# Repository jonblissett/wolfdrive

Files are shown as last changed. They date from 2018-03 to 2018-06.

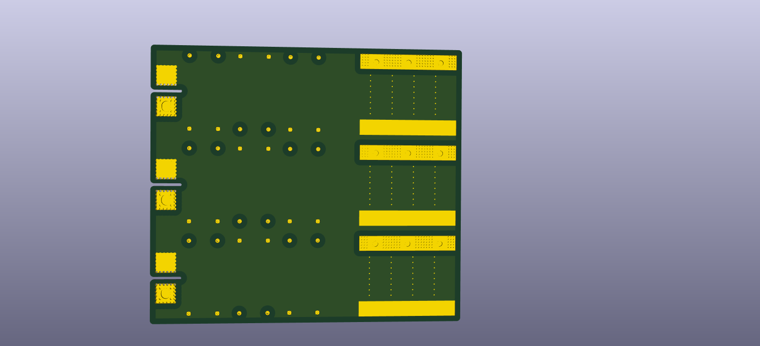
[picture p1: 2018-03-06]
DCbus/WolfDrive_DCbus_fab/WolfDrive_DCbus_back.png

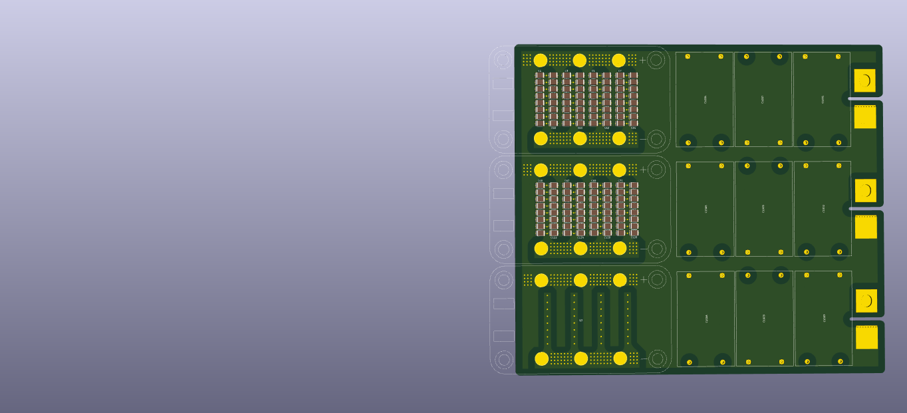
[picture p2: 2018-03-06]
DCbus/WolfDrive_DCbus.png

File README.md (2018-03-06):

# wolfdrive
Motor drive inverter designed to be used with the Cree CAS325M12HM2 silicon carbide MOSFETs.

Anticipated specifications:
Peak power, 250kW
Current, ~300Arms
DC bus voltage, <800Vdc

## /controller

Control board, using STM32H743 microcontroller. Accepts analogue signals for throttle, will output FOC signals to gate drivers.

## /firmware

Software repository for controller - currently empty!

## /DCbus

PCB to connect DC bus capacitors with low stray inductance

## /DCsnubber

Alternative DC bus capacitor connection for small capacitors above devices like in early evaluation kit from Cree. May work out to be a cheaper option than /DCbus.

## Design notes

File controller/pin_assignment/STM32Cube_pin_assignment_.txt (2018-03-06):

Configuration	STM32Cube_pin_assignment_
STM32CubeMX 	4.23.0
Date	11/22/2017
MCU	STM32H743ZITx

PERIPHERALS	MODES	FUNCTIONS	PINS
ADC2	IN5 Single-ended	ADC2_INP5	PB1
ETH	RMII	ETH_CRS_DV	PA7
ETH	RMII	ETH_MDC	PC1
ETH	RMII	ETH_MDIO	PA2
ETH	RMII	ETH_REF_CLK	PA1
ETH	RMII	ETH_RXD0	PC4
ETH	RMII	ETH_RXD1	PC5
ETH	RMII	ETH_TXD0	PB12
ETH	RMII	ETH_TXD1	PB13
ETH	RMII	ETH_TX_EN	PB11
QUADSPI	Bank1 with Quad SPI Lines	QUADSPI_BK1_IO0	PD11
QUADSPI	Bank1 with Quad SPI Lines	QUADSPI_BK1_IO1	PD12
QUADSPI	Bank1 with Quad SPI Lines	QUADSPI_BK1_IO2	PE2
QUADSPI	Bank1 with Quad SPI Lines	QUADSPI_BK1_IO3	PD13
QUADSPI	Bank1 with Quad SPI Lines	QUADSPI_BK1_NCS	PB10
QUADSPI	Bank1 with Quad SPI Lines	QUADSPI_CLK	PB2
SDMMC1	SD 4 bits Wide bus	SDMMC1_CK	PC12
SDMMC1	SD 4 bits Wide bus	SDMMC1_CMD	PD2
SDMMC1	SD 4 bits Wide bus	SDMMC1_D0	PC8
SDMMC1	SD 4 bits Wide bus	SDMMC1_D1	PC9
SDMMC1	SD 4 bits Wide bus	SDMMC1_D2	PC10
SDMMC1	SD 4 bits Wide bus	SDMMC1_D3	PC11
SPI1	Full-Duplex Master	SPI1_MISO	PA6
SPI1	Full-Duplex Master	SPI1_MOSI	PD7
SPI1	Full-Duplex Master	SPI1_SCK	PA5
SPI1	Hardware NSS Output Signal	SPI1_NSS	PA15
SPI2	Full-Duplex Master	SPI2_MISO	PC2_C
SPI2	Full-Duplex Master	SPI2_MOSI	PB15
SPI2	Full-Duplex Master	SPI2_SCK	PD3
SPI2	Hardware NSS Output Signal	SPI2_NSS	PB4
SYS	Serial Wire	SYS_JTCK-SWCLK	PA14
SYS	Serial Wire	SYS_JTMS-SWDIO	PA13
SYS	SysTick	SYS_VS_Systick	VP_SYS_VS_Systick
TIM1	Internal Clock	TIM1_VS_ClockSourceINT	VP_TIM1_VS_ClockSourceINT
TIM1	PWM Generation CH1 CH1N	TIM1_CH1	PE9
TIM1	PWM Generation CH1 CH1N	TIM1_CH1N	PE8
TIM1	PWM Generation CH2 CH2N	TIM1_CH2	PE11
TIM1	PWM Generation CH2 CH2N	TIM1_CH2N	PE10
TIM1	Output Compare CH3 CH3N	TIM1_CH3	PE13
TIM1	Output Compare CH3 CH3N	TIM1_CH3N	PE12
USART6	Asynchronous	USART6_RX	PG9
USART6	Asynchronous	USART6_TX	PG14

Pin Nb	PINs	FUNCTIONs	LABELs
1	PE2	QUADSPI_BK1_IO2	
27	PC1	ETH_MDC	
28	PC2_C	SPI2_MISO	
35	PA1	ETH_REF_CLK	
36	PA2	ETH_MDIO	
41	PA5	SPI1_SCK	
42	PA6	SPI1_MISO	
43	PA7	ETH_CRS_DV	
44	PC4	ETH_RXD0	
45	PC5	ETH_RXD1	
47	PB1	ADC2_INP5	
48	PB2	QUADSPI_CLK	
59	PE8	TIM1_CH1N	
60	PE9	TIM1_CH1	
63	PE10	TIM1_CH2N	
64	PE11	TIM1_CH2	
65	PE12	TIM1_CH3N	
66	PE13	TIM1_CH3	
69	PB10	QUADSPI_BK1_NCS	
70	PB11	ETH_TX_EN	
73	PB12	ETH_TXD0	
74	PB13	ETH_TXD1	
76	PB15	SPI2_MOSI	
80	PD11	QUADSPI_BK1_IO0	
81	PD12	QUADSPI_BK1_IO1	
82	PD13	QUADSPI_BK1_IO3	
98	PC8	SDMMC1_D0	
99	PC9	SDMMC1_D1	
105	PA13	SYS_JTMS-SWDIO	
109	PA14	SYS_JTCK-SWCLK	
110	PA15	SPI1_NSS	
111	PC10	SDMMC1_D2	
112	PC11	SDMMC1_D3	
113	PC12	SDMMC1_CK	
116	PD2	SDMMC1_CMD	
117	PD3	SPI2_SCK	
123	PD7	SPI1_MOSI	
124	PG9	USART6_RX	
129	PG14	USART6_TX	
134	PB4	SPI2_NSS

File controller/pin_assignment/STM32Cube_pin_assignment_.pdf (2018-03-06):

## STM32Cube_pin_assignment_ Project Configuration Report

# 1. Description

## 1.1. Project

Project Name | STM32Cube_pin_assignment_
Board Name | No information
Generated with: | STM32CubeMX 4.23.0
Date | 11/22/2017

## 1.2. MCU

MCU Series | STM32H7
MCU Line | STM32H7x3
MCU name | STM32H743ZITx
MCU Package | LQFP144
MCU Pin number | 144

# 2. Pinout Configuration

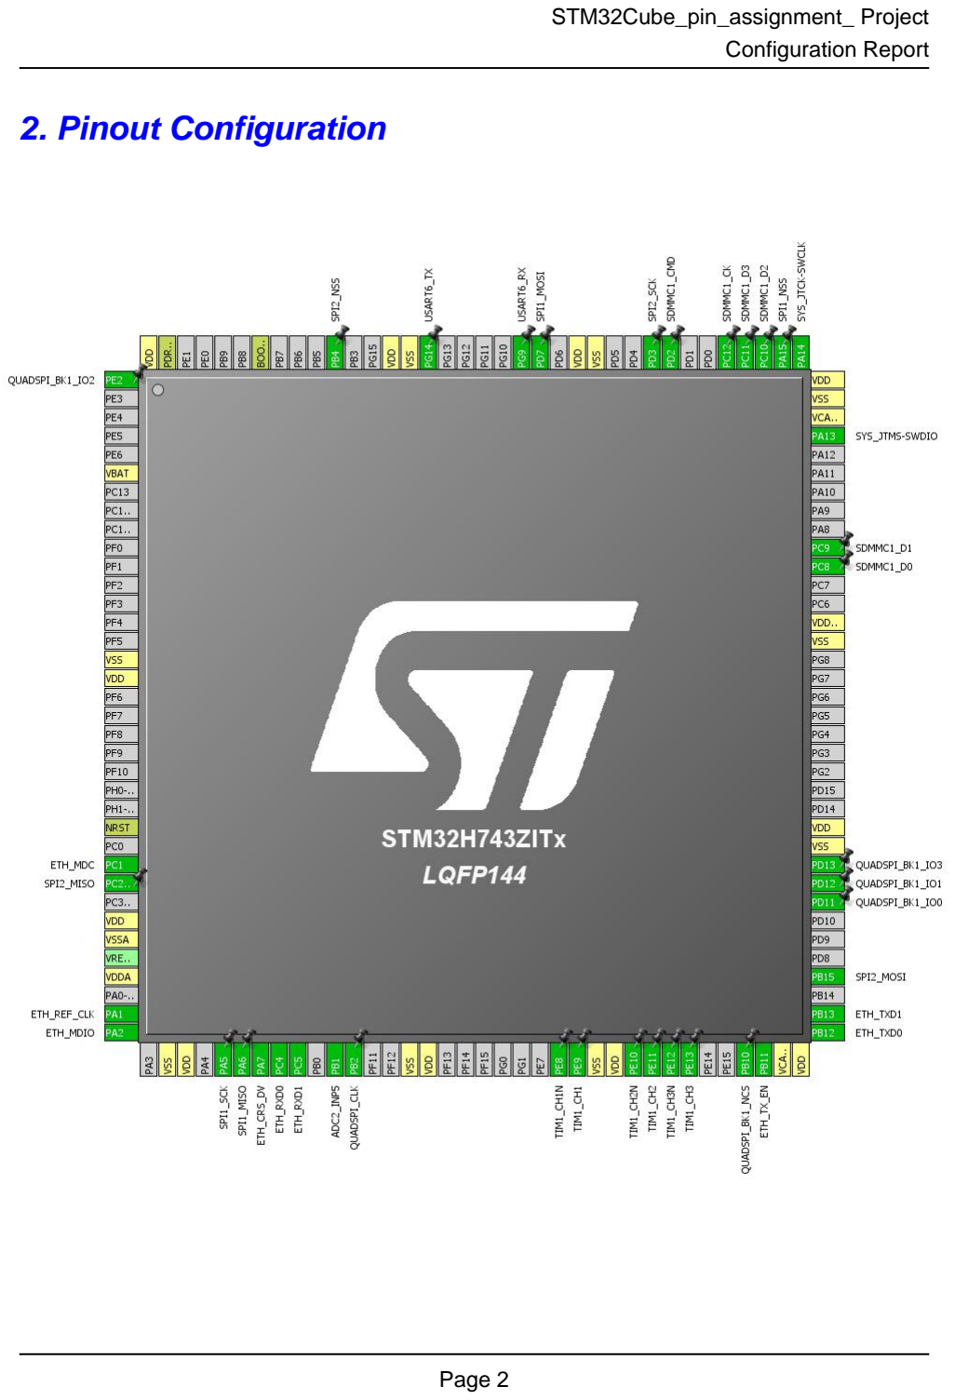
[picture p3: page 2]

# 3. Pins Configuration

Pin Number LQFP144 | Pin Name (function after reset) | Pin Type | Alternate Function(s) | Label
1 | PE2 | I/O | QUADSPI_BK1_IO2
6 | VBAT | Power
16 | VSS | Power
17 | VDD | Power
25 | NRST | Reset
27 | PC1 | I/O | ETH_MDC
28 | PC2_C | I/O | SPI2_MISO
30 | VDD | Power
31 | VSSA | Power
33 | VDDA | Power
35 | PA1 | I/O | ETH_REF_CLK
36 | PA2 | I/O | ETH_MDIO
38 | VSS | Power
39 | VDD | Power
41 | PA5 | I/O | SPI1_SCK
42 | PA6 | I/O | SPI1_MISO
43 | PA7 | I/O | ETH_CRS_DV
44 | PC4 | I/O | ETH_RXD0
45 | PC5 | I/O | ETH_RXD1
47 | PB1 | I/O | ADC2_INP5
48 | PB2 | I/O | QUADSPI_CLK
51 | VSS | Power
52 | VDD | Power
59 | PE8 | I/O | TIM1_CH1N
60 | PE9 | I/O | TIM1_CH1
61 | VSS | Power
62 | VDD | Power
63 | PE10 | I/O | TIM1_CH2N
64 | PE11 | I/O | TIM1_CH2
65 | PE12 | I/O | TIM1_CH3N
66 | PE13 | I/O | TIM1_CH3
69 | PB10 | I/O | QUADSPI_BK1_NCS
70 | PB11 | I/O | ETH_TX_EN
71 | VCAP1 | Power
72 | VDD | Power
73 | PB12 | I/O | ETH_TXD0

Pin Number LQFP144 | Pin Name (function after reset) | Pin Type | Alternate Function(s) | Label
74 | PB13 | I/O | ETH_TXD1
76 | PB15 | I/O | SPI2_MOSI
80 | PD11 | I/O | QUADSPI_BK1_IO0
81 | PD12 | I/O | QUADSPI_BK1_IO1
82 | PD13 | I/O | QUADSPI_BK1_IO3
83 | VSS | Power
84 | VDD | Power
94 | VSS | Power
95 | VDD33_USB | Power
98 | PC8 | I/O | SDMMC1_D0
99 | PC9 | I/O | SDMMC1_D1
105 | PA13 | I/O | SYS_JTMS-SWDIO
106 | VCAP2 | Power
107 | VSS | Power
108 | VDD | Power
109 | PA14 | I/O | SYS_JTCK-SWCLK
110 | PA15 | I/O | SPI1_NSS
111 | PC10 | I/O | SDMMC1_D2
112 | PC11 | I/O | SDMMC1_D3
113 | PC12 | I/O | SDMMC1_CK
116 | PD2 | I/O | SDMMC1_CMD
117 | PD3 | I/O | SPI2_SCK
120 | VSS | Power
121 | VDD | Power
123 | PD7 | I/O | SPI1_MOSI
124 | PG9 | I/O | USART6_RX
129 | PG14 | I/O | USART6_TX
130 | VSS | Power
131 | VDD | Power
134 | PB4 | I/O | SPI2_NSS
138 | BOOT0 | Boot
143 | PDR_ON | Reset
144 | VDD | Power

# 4. Clock Tree Configuration

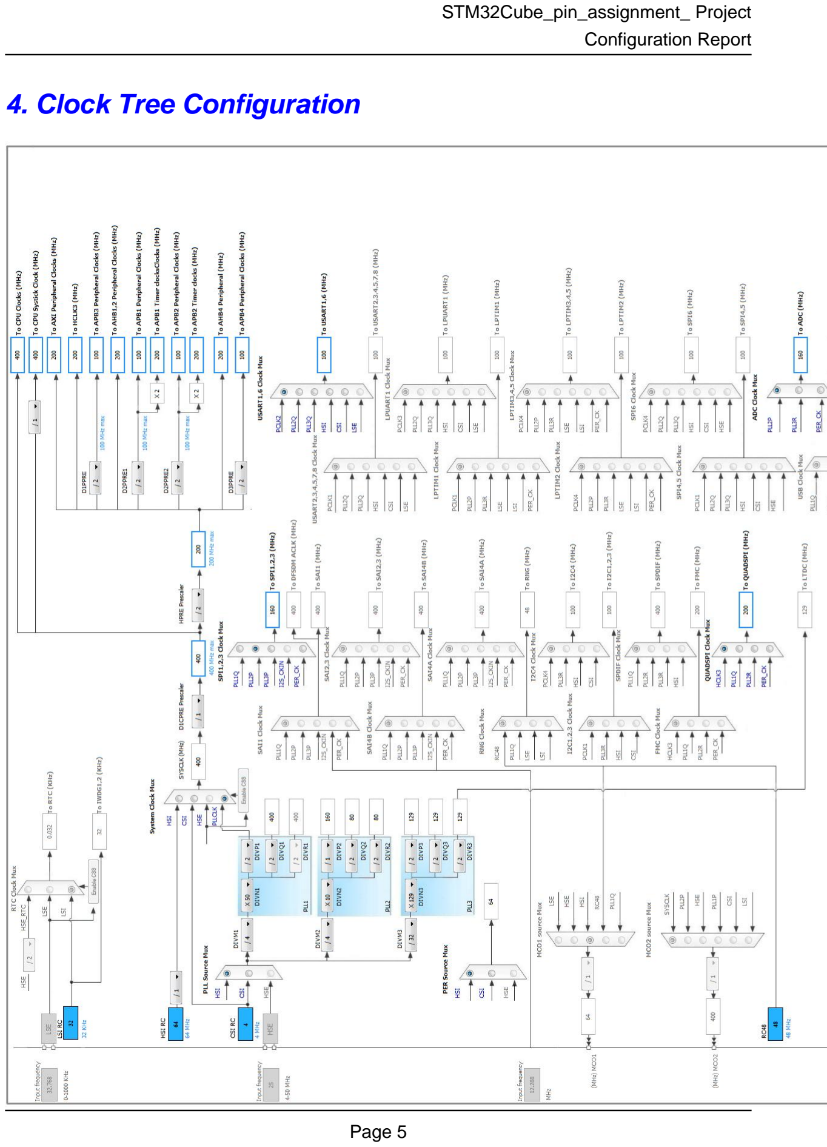
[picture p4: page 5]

# 5. IPs and Middleware Configuration

# 5.1. ADC2

## IN5: IN5 Single-ended

## 5.1.1. Parameter Settings:

### ADCs_Common_Settings:

Mode | Independent mode

### ADC_Settings:

Clock Prescaler | Asynchronous clock mode divided by 6
Resolution | ADC 16-bit resolution
Scan Conversion Mode | Disabled
Continuous Conversion Mode | Disabled
Discontinuous Conversion Mode | Disabled
DMA Continuous Requests | Disabled
End Of Conversion Selection | End of single conversion
Overrun behaviour | Overrun data preserved
Boost Mode | Enabled
Conversion Data Management Mode | Regular Conversion data stored in DR register only
Low Power Auto Wait | Disabled

### ADC_Regular_ConversionMode:

Enable Regular Conversions | Enable
Left Bit Shift | No bit shift
Enable Regular Oversampling | Disable
Number Of Conversion | 1
External Trigger Conversion Source | Regular Conversion launched by software
External Trigger Conversion Edge | None
Rank | 1
Channel | Channel 5
Sampling Time | 1.5 Cycles
Offset Number | No offset

### ADC_Injected_ConversionMode:

Enable Injected Conversions | Disable

### Analog Watchdog 1:

Enable Analog WatchDog1 Mode | false

### Analog Watchdog 2:

Enable Analog WatchDog2 Mode | false

### Analog Watchdog 3:

Enable Analog WatchDog3 Mode | false

# 5.2. ETH

## Mode: RMII

## 5.2.1. Parameter Settings:

### General : Ethernet Configuration:

Warning | The ETH can work only when RAM is pointing at 0x24000000
Note | PHY Driver must be configured from the LwIP 'Platform Settings' top right tab
Ethernet MAC Address | 00:80:E1:00:00:00
Tx Descriptor Length | 4
First Tx Descriptor Address | 0x30040060 *
Rx Descriptor Length | 4
First Rx Descriptor Address | 0x30040000 *
Rx Buffers Address | 0x30040200 *
Rx Buffers Length | 1524

# 5.3. QUADSPI

## QuadSPI Mode: Bank1 with Quad SPI Lines

## 5.3.1. Parameter Settings:

### General Parameters:

Clock Prescaler | 255
Fifo Threshold | 1
Sample Shifting | No Sample Shifting
Flash Size | 1
Chip Select High Time | 1 Cycle
Clock Mode | Low
Flash ID | Flash ID 1
Dual Flash | Disabled

# 5.4. SDMMC1

## Mode: SD 4 bits Wide bus

## 5.4.1. Parameter Settings:

### SDMMC parameters:

Clock transition on which the bit capture is made | Rising transition
SDMMC Clock output enable when the bus is idle | Disable the power save for the clock
SDMMC hardware flow control | The hardware control flow is disabled
SDMMCCLK clock divide factor | 0

# 5.5. SPI1

## Mode: Full-Duplex Master Hardware NSS Signal: Hardware NSS Output Signal

## 5.5.1. Parameter Settings:

### Basic Parameters:

Frame Format | Motorola
Data Size | 4 Bits
First Bit | MSB First

### Clock Parameters:

Prescaler (for Baud Rate) | 32 *
Baud Rate | 5.0 MBits/s *
Clock Polarity (CPOL) | Low
Clock Phase (CPHA) | 1 Edge

### Advanced Parameters:

CRC Calculation | Disabled
NSSP Mode | Enabled
NSS Signal Type | Output Hardware
Fifo Threshold | Fifo Threshold 01 Data
Tx Crc Initialization Pattern | All Zero Pattern
Rx Crc Initialization Pattern | All Zero Pattern
Nss Polarity | Nss Polarity Low
Master Ss Idleness | 00 Cycle
Master Inter Data Idleness | 00 Cycle
Master Receiver Auto Susp | 00 Cycle
Master Keep IO State | 0
IO Swap | Disabled

# 5.6. SPI2

## Mode: Full-Duplex Master Hardware NSS Signal: Hardware NSS Output Signal

## 5.6.1. Parameter Settings:

### Basic Parameters:

Frame Format | Motorola
Data Size | 4 Bits
First Bit | MSB First

### Clock Parameters:

Prescaler (for Baud Rate) | 32 *
Baud Rate | 5.0 MBits/s *
Clock Polarity (CPOL) | Low
Clock Phase (CPHA) | 1 Edge

### Advanced Parameters:

CRC Calculation | Disabled
NSSP Mode | Enabled
NSS Signal Type | Output Hardware
Fifo Threshold | Fifo Threshold 01 Data
Tx Crc Initialization Pattern | All Zero Pattern
Rx Crc Initialization Pattern | All Zero Pattern
Nss Polarity | Nss Polarity Low
Master Ss Idleness | 00 Cycle
Master Inter Data Idleness | 00 Cycle
Master Receiver Auto Susp | 00 Cycle
Master Keep IO State | 0
IO Swap | Disabled

# 5.7. SYS

## Debug: Serial Wire Timebase Source: SysTick

# 5.8. TIM1

## Clock Source : Internal Clock Channel1: PWM Generation CH1 CH1N Channel2: PWM Generation CH2 CH2N Channel3: Output Compare CH3 CH3N

## 5.8.1. Parameter Settings:

### Counter Settings:

Prescaler (PSC - 16 bits value) | 0
Counter Mode | Up
Counter Period (AutoReload Register - 16 bits value ) | 0
Internal Clock Division (CKD) | No Division
Repetition Counter (RCR - 16 bits value) | 0
auto-reload preload | Disable

### Trigger Output (TRGO) Parameters:

Master/Slave Mode | Disable (no sync between this TIM (Master) and its Slaves
Trigger Event Selection TRGO | Reset (UG bit from TIMx_EGR)
Trigger Event Selection TRGO2 | Reset (UG bit from TIMx_EGR)

### Break And Dead Time management - BRK Configuration:

BRK State | Disable
BRK Polarity | High
BRK Filter (4 bits value) | 0
BRK Sources Configuration
- Digital Input | Disable
- COMP1 | Disable
- COMP2 | Disable
- DFSDM | Disable

### Break And Dead Time management - BRK2 Configuration:

BRK2 State | Disable
BRK2 Polarity | High
BRK2 Filter (4 bits value) | 0
BRK2 Sources Configuration
- Digital Input | Disable
- COMP1 | Disable
- COMP2 | Disable
- DFSDM | Disable

### Break And Dead Time management - Output Configuration:

Automatic Output State | Disable
Off State Selection for Run Mode (OSSR) | Disable
Off State Selection for Idle Mode (OSSI) | Disable
Lock Configuration | Off

Dead Time | 0

### Clear Input:

Clear Input Source | Disable

### PWM Generation Channel 1 and 1N:

Mode | PWM mode 1
Pulse (16 bits value) | 0
Fast Mode | Disable
CH Polarity | High
CHN Polarity | High
CH Idle State | Reset
CHN Idle State | Reset

### PWM Generation Channel 2 and 2N:

Mode | PWM mode 1
Pulse (16 bits value) | 0
Fast Mode | Disable
CH Polarity | High
CHN Polarity | High
CH Idle State | Reset
CHN Idle State | Reset

### Output Compare Channel 3 and 3N:

Mode | Frozen (used for Timing base)
Pulse (16 bits value) | 0
CH Polarity | High
CHN Polarity | High
CH Idle State | Reset
CHN Idle State | Reset

# 5.9. USART6

## Mode: Asynchronous

## 5.9.1. Parameter Settings:

### Basic Parameters:

Baud Rate | 115200
Word Length | 7 Bits (including Parity)
Parity | None
Stop Bits | 1

### Advanced Parameters:

Data Direction | Receive and Transmit

Over Sampling | 16 Samples
Single Sample | Disable
Prescaler | clock /1
Fifo Mode | Disable
Txfifo Threshold | 1 eighth full configuration
Rxfifo Threshold | 1 eighth full configuration

### Advanced Features:

Auto Baudrate | Disable
TX Pin Active Level Inversion | Disable
RX Pin Active Level Inversion | Disable
Data Inversion | Disable
TX and RX Pins Swapping | Disable
Overrun | Enable
DMA on RX Error | Enable
MSB First | Disable

### * User modified value

# 6. System Configuration

# 6.1. GPIO configuration

IP | Pin | Signal | GPIO mode | GPIO pull/up pull down

## Max Speed

## User Label

ADC2 | PB1 | ADC2_INP5 | Analog mode | No pull-up and no pull-down | n/a
ETH | PC1 | ETH_MDC | Alternate Function Push Pull | No pull-up and no pull-down | Low
PA1 | ETH_REF_CLK Alternate Function Push Pull | No pull-up and no pull-down | Low
| PA2 | ETH_MDIO | Alternate Function Push Pull | No pull-up and no pull-down | Low
PA7 | ETH_CRS_DV Alternate Function Push Pull | No pull-up and no pull-down | Low
| PC4 | ETH_RXD0 | Alternate Function Push Pull | No pull-up and no pull-down | Low
| PC5 | ETH_RXD1 | Alternate Function Push Pull | No pull-up and no pull-down | Low
| PB11 | ETH_TX_EN | Alternate Function Push Pull | No pull-up and no pull-down | Low
| PB12 | ETH_TXD0 | Alternate Function Push Pull | No pull-up and no pull-down | Low
| PB13 | ETH_TXD1 | Alternate Function Push Pull | No pull-up and no pull-down | Low
QUADSPI | PE2 | QUADSPI_BK1_I O2 | Alternate Function Push Pull | No pull-up and no pull-down | Low
PB2 | QUADSPI_CLK Alternate Function Push Pull | No pull-up and no pull-down | Low
| PB10 | QUADSPI_BK1_ NCS | Alternate Function Push Pull | No pull-up and no pull-down | Low
| PD11 | QUADSPI_BK1_I O0 | Alternate Function Push Pull | No pull-up and no pull-down | Low
| PD12 | QUADSPI_BK1_I O1 | Alternate Function Push Pull | No pull-up and no pull-down | Low
| PD13 | QUADSPI_BK1_I O3 | Alternate Function Push Pull | No pull-up and no pull-down | Low
SDMMC1 | PC8 | SDMMC1_D0 | Alternate Function Push Pull | No pull-up and no pull-down | Very High
| PC9 | SDMMC1_D1 | Alternate Function Push Pull | No pull-up and no pull-down | Very High
| PC10 | SDMMC1_D2 | Alternate Function Push Pull | No pull-up and no pull-down | Very High
| PC11 | SDMMC1_D3 | Alternate Function Push Pull | No pull-up and no pull-down | Very High
PC12 | SDMMC1_CK Alternate Function Push Pull | No pull-up and no pull-down | Very High
PD2 | SDMMC1_CMD Alternate Function Push Pull | No pull-up and no pull-down | Very High
SPI1 | PA5 | SPI1_SCK | Alternate Function Push Pull | No pull-up and no pull-down | Low
| PA6 | SPI1_MISO | Alternate Function Push Pull | No pull-up and no pull-down | Low
| PA15 | SPI1_NSS | Alternate Function Push Pull | No pull-up and no pull-down | Low
| PD7 | SPI1_MOSI | Alternate Function Push Pull | No pull-up and no pull-down | Low
SPI2 | PC2_C | SPI2_MISO | Alternate Function Push Pull | No pull-up and no pull-down | Low
| PB15 | SPI2_MOSI | Alternate Function Push Pull | No pull-up and no pull-down | Low
| PD3 | SPI2_SCK | Alternate Function Push Pull | No pull-up and no pull-down | Low
| PB4 | SPI2_NSS | Alternate Function Push Pull | No pull-up and no pull-down | Low

IP | Pin | Signal | GPIO mode | GPIO pull/up pull down | Max Speed | User Label
SYS | PA13 | SYS_JTMS-SWDIO | n/a | n/a | n/a
| PA14 | SYS_JTCK-SWCLK | n/a | n/a | n/a
TIM1 | PE8 | TIM1_CH1N | Alternate Function Push Pull | No pull-up and no pull-down | Low
| PE9 | TIM1_CH1 | Alternate Function Push Pull | No pull-up and no pull-down | Low
| PE10 | TIM1_CH2N | Alternate Function Push Pull | No pull-up and no pull-down | Low
| PE11 | TIM1_CH2 | Alternate Function Push Pull | No pull-up and no pull-down | Low
| PE12 | TIM1_CH3N | Alternate Function Push Pull | No pull-up and no pull-down | Low
| PE13 | TIM1_CH3 | Alternate Function Push Pull | No pull-up and no pull-down | Low
USART6 | PG9 | USART6_RX | Alternate Function Push Pull | Pull-up | Low
| PG14 | USART6_TX | Alternate Function Push Pull | Pull-up | Low

# 6.2. DMA configuration

## nothing configured in DMA service

# 6.3. BDMA configuration

## nothing configured in DMA service

# 6.4. MDMA configuration

## nothing configured in DMA service

# 6.5. NVIC configuration

Interrupt Table | Enable | Preenmption Priority | SubPriority
Non maskable interrupt | true | 0 | 0
Hard fault interrupt | true | 0 | 0
Memory management fault | true | 0 | 0
Pre-fetch fault, memory access fault | true | 0 | 0
Undefined instruction or illegal state | true | 0 | 0
System service call via SWI instruction | true | 0 | 0
Debug monitor | true | 0 | 0
Pendable request for system service | true | 0 | 0
System tick timer | true | 0 | 0
PVD and AVD interrupts through EXTI line 16 | unused
Flash global interrupt | unused
RCC global interrupt | unused
ADC1 and ADC2 global interrupts | unused
TIM1 break interrupt | unused
TIM1 update interrupt | unused
TIM1 trigger and commutation interrupts | unused
TIM1 capture compare interrupt | unused
SPI1 global interrupt | unused
SPI2 global interrupt | unused
SDMMC1 global interrupt | unused
Ethernet global interrupt | unused
Ethernet wake-up interrupt through EXTI line 86 | unused
USART6 global interrupt | unused
FPU global interrupt | unused
QUADSPI global interrupt | unused
HSEM1 global interrupt | unused

### * User modified value

# 7. Power Consumption Calculator report

### 7.1. Microcontroller Selection

Series | STM32H7
Line | STM32H7x3
MCU | STM32H743ZITx
Datasheet | 030538_Rev1

### 7.2. Parameter Selection

Temperature | 25
Vdd | 3.0

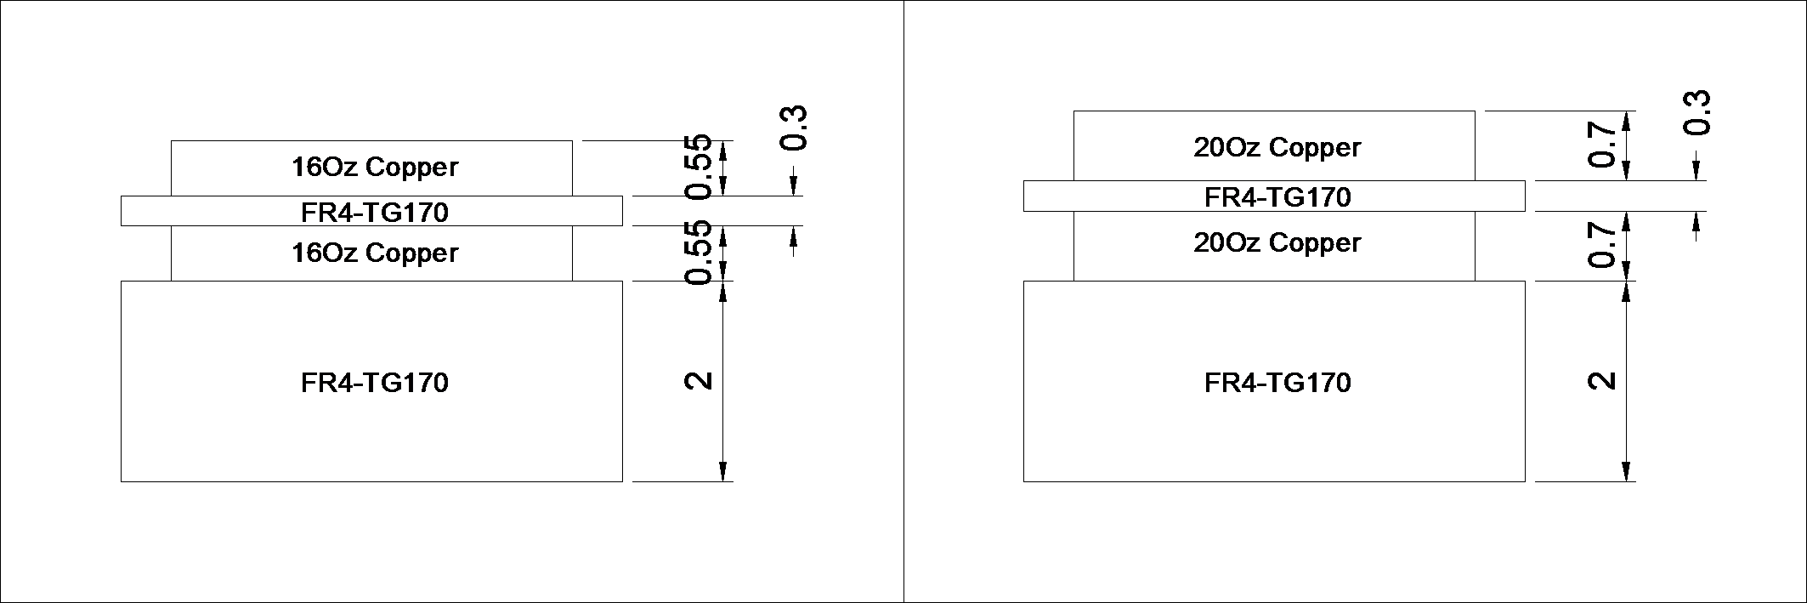
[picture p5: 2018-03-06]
DCbus/drawings/wolf_stackup_2.png

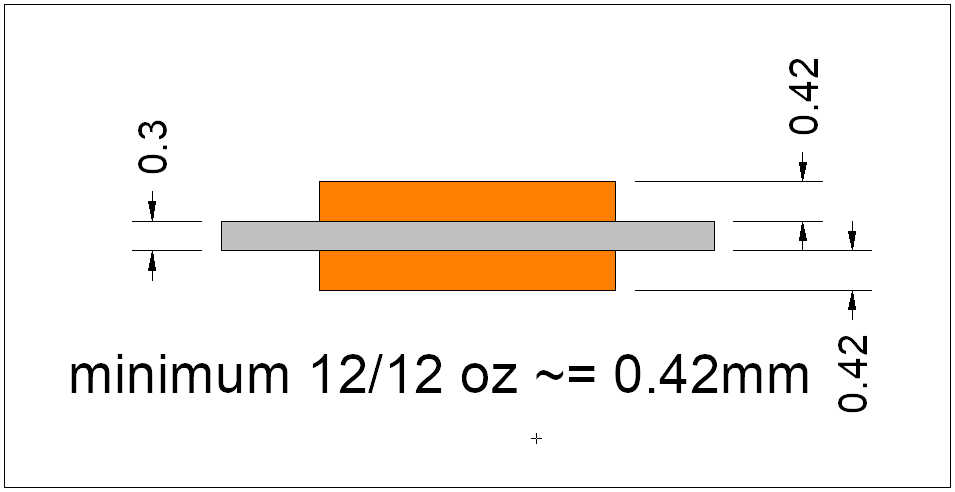
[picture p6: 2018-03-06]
DCbus/WolfDrive_DCbus_fab/pcb_stack.png

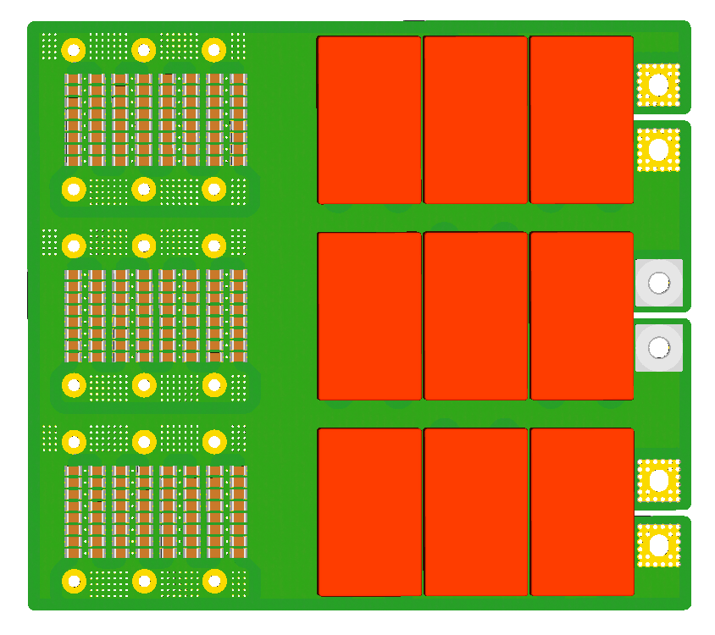
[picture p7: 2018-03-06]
DCbus/WolfDrive_DCbus_3D_3.png

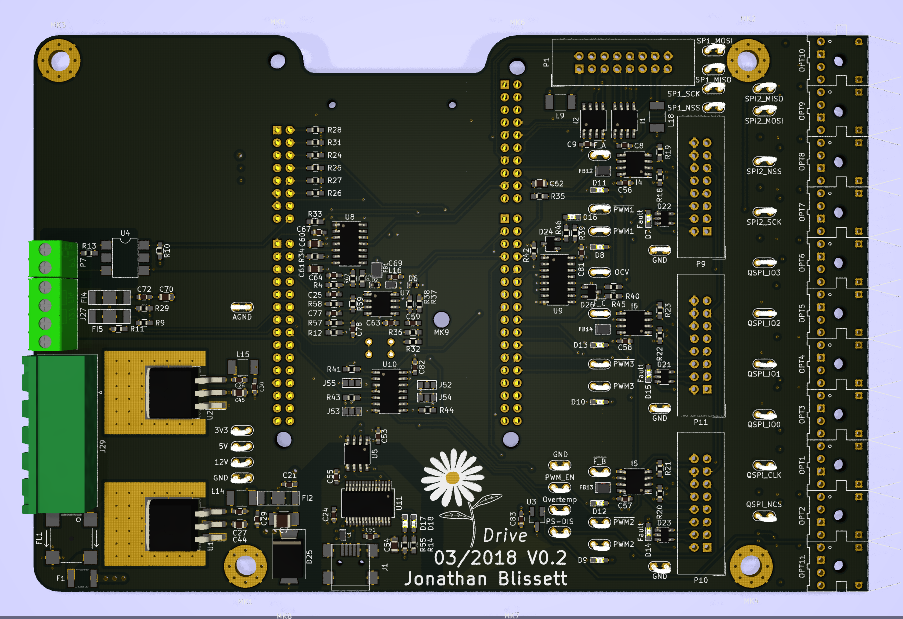
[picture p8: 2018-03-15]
controller/WolfDrive_H7Controller/WolfDrive_H7Controller.png

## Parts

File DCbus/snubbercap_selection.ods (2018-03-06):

V = | 700 |  |  |  |  |  | http://ksim.kemet.com/Plots/SpicePlots.aspx
X7R | 0.143
C0G | 1
Dielectric | Package | easy fit | squeeze | C nominal | C @ V | C, Easy | C, Squeeze | Part # | £ | £
C0G | 4540 | 12 | 13 | 68 | 68.0 | 816 | 884 | C4540H683JDGACT050 | 15.91 | 620.49
C0G | 3640 | 14 | 17 | 47 | 47.0 | 658 | 799 | C3640C473JDGACAUTO | 8.37 | 426.87
X7R | 2225 | 26 | 28 | 150 | 21.5 | 558 | 601 | C2225X154KDRACTU | 1.14 | 95.76
X7R | 1825 | 28 | 28 | 100 | 14.3 | 400 | 400 | C1825X104KDRACTU | 0.737 | 61.908
X7R | 1812 | 56 | 63 | 100 | 14.3 | 801 | 901 | C1812W104KDRACTU | 0.354 | 66.906 | http://uk.farnell.com/kemet/c1812w104kdractu/cap-mlcc-x7r-100nf-1kv-1812/dp/2085229?CMP=GRHB-OCTOPART
 |  |  |  |  |  |  | 976
 | For 1812:
 | The non-coated group capacitors showed arc– over at approximately 1200VDC and the ramp was halted due to the instruments arc-over detection function. Although no external physical defects were present, post insulation resistance measurements showed that 37% of the non-coated parts had unacceptable insulation resistance. The conformal coated group of capacitors failed at approximately 3660 VDC and had signs of external damage.
 | https://www.vishay.com/docs/49726/49726.pdf

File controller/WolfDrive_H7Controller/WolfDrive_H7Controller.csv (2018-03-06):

Reference | Value | Footprint | Datasheet
C44 | 10u, 10v | Capacitors_SMD:C_0805
C27 | 100n | Capacitors_SMD:C_0603_HandSoldering
C7 | 22u, 16V | Capacitors_SMD:C_1210
FI2 | NFE61P | DriveParts:EMI_Filter_murata
C63 | 47n | Capacitors_SMD:C_0603_HandSoldering
R32 | DNP | Resistors_SMD:R_0603_HandSoldering
R36 | DNP | Resistors_SMD:R_0603_HandSoldering
C59 | 47n | Capacitors_SMD:C_0603_HandSoldering
R38 | 0R | Resistors_SMD:R_0603_HandSoldering
R37 | DNP | Resistors_SMD:R_0603_HandSoldering
R30 | DNP | Resistors_SMD:R_0603_HandSoldering
R29 | DNP | Resistors_SMD:R_0603_HandSoldering
C45 | 10u, 6.3v | Capacitors_SMD:C_0805
D6 | 3.3V | Diodes_SMD:D_SOD-523
C28 | 100n | Capacitors_SMD:C_0603_HandSoldering
C30 | 10n | Capacitors_SMD:C_0603_HandSoldering
C29 | 1u | Capacitors_SMD:C_0603_HandSoldering
L14 | 10uH | Inductors_NEOSID:Neosid_Inductor_SM-NE30_SMD1210
L15 | 10uH | Inductors_NEOSID:Neosid_Inductor_SM-NE30_SMD1210
C21 | 1n | Capacitors_SMD:C_0603_HandSoldering
OPT11 | AFBR-26x | DriveParts:HFBR-xx2xZ
C79 | 10u | Capacitors_SMD:C_0805
C75 | 10u | Capacitors_SMD:C_0805
L17 | 1uH | w_smd_inductors:inductor_smd_0603
C80 | 100n | Capacitors_SMD:C_0603_HandSoldering
I7 | DS90LV027A | Housings_SOIC:SOIC-8_3.9x4.9mm_Pitch1.27mm
C76 | 100n | Capacitors_SMD:C_0603_HandSoldering
I1 | DS90LV027A | SMD_Packages:SOIC-8-N
C8 | 100n | Capacitors_SMD:C_0603_HandSoldering
I3 | DS90LV028A | SMD_Packages:SOIC-8-N
R8 | 250 | Resistors_SMD:R_0603_HandSoldering
C35 | 100n | Capacitors_SMD:C_0603_HandSoldering
CON1 | SD_Card | Connectors:SD_Card_Receptacle
I4 | DS90LV028A | Housings_SOIC:SOIC-8_3.9x4.9mm_Pitch1.27mm
R19 | 240 | Resistors_SMD:R_0603_HandSoldering
R18 | 240 | Resistors_SMD:R_0603_HandSoldering
C56 | 100n | Capacitors_SMD:C_0603_HandSoldering
C37 | 10u | Capacitors_SMD:C_0805
C32 | 10u | Capacitors_SMD:C_0805
R5 | 4k7 | Resistors_SMD:R_0603_HandSoldering
L11 | 1uH | w_smd_inductors:inductor_smd_0603
OPT7 | AFBR-1634Z | DriveParts:HFBR-xx2xZ
C41 | 100n | Capacitors_SMD:C_0603_HandSoldering
R6 | 4k7 | Resistors_SMD:R_0603_HandSoldering
OPT10 | AFBR-26x | DriveParts:HFBR-xx2xZ
R7 | 4k7 | Resistors_SMD:R_0603_HandSoldering
C38 | 10u | Capacitors_SMD:C_0805
C33 | 10u | Capacitors_SMD:C_0805
L12 | 1uH | w_smd_inductors:inductor_smd_0603
OPT8 | AFBR-1634Z | DriveParts:HFBR-xx2xZ
C42 | 100n | Capacitors_SMD:C_0603_HandSoldering
C39 | 10u | Capacitors_SMD:C_0805
C34 | 10u | Capacitors_SMD:C_0805
L13 | 1uH | w_smd_inductors:inductor_smd_0603
OPT9 | AFBR-1634Z | DriveParts:HFBR-xx2xZ
C43 | 100n | Capacitors_SMD:C_0603_HandSoldering
C36 | 10u | Capacitors_SMD:C_0805
C31 | 10u | Capacitors_SMD:C_0805
L10 | 1uH | w_smd_inductors:inductor_smd_0603
C40 | 100n | Capacitors_SMD:C_0603_HandSoldering
C15 | 10u | Capacitors_SMD:C_0805
C5 | 10u | Capacitors_SMD:C_0805
R1 | 4k7 | Resistors_SMD:R_0603_HandSoldering
L6 | 1uH | w_smd_inductors:inductor_smd_0603
OPT1 | AFBR-1634Z | DriveParts:HFBR-xx2xZ
C22 | 100n | Capacitors_SMD:C_0603_HandSoldering
R2 | 4k7 | Resistors_SMD:R_0603_HandSoldering
OPT3 | AFBR-26x | DriveParts:HFBR-xx2xZ
C16 | 10u | Capacitors_SMD:C_0805
C6 | 10u | Capacitors_SMD:C_0805
L7 | 1uH | w_smd_inductors:inductor_smd_0603
OPT2 | AFBR-1634Z | DriveParts:HFBR-xx2xZ
C23 | 100n | Capacitors_SMD:C_0603_HandSoldering
C11 | 10u | Capacitors_SMD:C_0805
C1 | 10u | Capacitors_SMD:C_0805
L2 | 1uH | w_smd_inductors:inductor_smd_0603
C17 | 100n | Capacitors_SMD:C_0603_HandSoldering
OPT4 | AFBR-26x | DriveParts:HFBR-xx2xZ
C12 | 10u | Capacitors_SMD:C_0805
C2 | 10u | Capacitors_SMD:C_0805
L3 | 1uH | w_smd_inductors:inductor_smd_0603
C18 | 100n | Capacitors_SMD:C_0603_HandSoldering
OPT5 | AFBR-26x | DriveParts:HFBR-xx2xZ
C13 | 10u | Capacitors_SMD:C_0805
C3 | 10u | Capacitors_SMD:C_0805
L4 | 1uH | w_smd_inductors:inductor_smd_0603
C19 | 100n | Capacitors_SMD:C_0603_HandSoldering
OPT6 | AFBR-26x | DriveParts:HFBR-xx2xZ
C14 | 10u | Capacitors_SMD:C_0805
C4 | 10u | Capacitors_SMD:C_0805
L5 | 1uH | w_smd_inductors:inductor_smd_0603
C20 | 100n | Capacitors_SMD:C_0603_HandSoldering
R51 | 0 | Resistors_SMD:R_0603_HandSoldering
FB6 | FILTER | w_smd_inductors:inductor_smd_0805
FB7 | FILTER | w_smd_inductors:inductor_smd_0805
FB8 | FILTER | w_smd_inductors:inductor_smd_0805
FB9 | FILTER | w_smd_inductors:inductor_smd_0805
FB10 | FILTER | w_smd_inductors:inductor_smd_0805
FB11 | FILTER | w_smd_inductors:inductor_smd_0805
R24 | 47k | Resistors_SMD:R_0603_HandSoldering
R25 | 47k | Resistors_SMD:R_0603_HandSoldering
R26 | 47k | Resistors_SMD:R_0603_HandSoldering
R27 | 47k | Resistors_SMD:R_0603_HandSoldering
R28 | 47k | Resistors_SMD:R_0603_HandSoldering
R31 | 47k | Resistors_SMD:R_0603_HandSoldering
C73 | 100n | Capacitors_SMD:C_0603_HandSoldering
C74 | 10u | Capacitors_SMD:C_0805
C71 | 100n | Capacitors_SMD:C_0603_HandSoldering
U5 | ISO7221 | Housings_SOIC:SOIC-8_3.9x4.9mm_Pitch1.27mm
C53 | 100n | Capacitors_SMD:C_0603_HandSoldering
C55 | 100n | Capacitors_SMD:C_0603_HandSoldering
U4 | LTV-356T | Housings_DIP:DIP-6_W7.62mm_SMD
R13 | 1k | Resistors_SMD:R_0603_HandSoldering
P7 | CONN_01X02 | Connectors_Terminal_Blocks:TerminalBlock_Pheonix_PT-3.5mm_2pol
R10 | 4k7 | Resistors_SMD:R_0603_HandSoldering
I2 | DS90LV027A | SMD_Packages:SOIC-8-N
C9 | 100n | Capacitors_SMD:C_0603_HandSoldering
R45 | 10k | Resistors_SMD:R_0603_HandSoldering
R46 | 10k | Resistors_SMD:R_0603_HandSoldering
U10 | 74LS136 | Housings_SOIC:SOIC-14_3.9x8.7mm_Pitch1.27mm
R47 | 10k | Resistors_SMD:R_0603_HandSoldering
R48 | 10k | Resistors_SMD:R_0603_HandSoldering
R43 | 10k | Resistors_SMD:R_0603_HandSoldering
R41 | 10k | Resistors_SMD:R_0603_HandSoldering
R42 | 10k | Resistors_SMD:R_0603_HandSoldering
R49 | 10k | Resistors_SMD:R_0603_HandSoldering
R50 | 10k | Resistors_SMD:R_0603_HandSoldering
R44 | 10k | Resistors_SMD:R_0603_HandSoldering
C81 | 100n | Capacitors_SMD:C_0603_HandSoldering
U9 | CD4044B | Housings_SOIC:SOIC-16_3.9x9.9mm_Pitch1.27mm
R54 | 47 | Resistors_SMD:R_0805
D7 | Led_Small | LEDs:LED_0603_HandSoldering
Q2 | Q_NMOS_DGS | w_smd_trans:sot23
R39 | 10k | Resistors_SMD:R_0603_HandSoldering
R40 | 10k | Resistors_SMD:R_0603_HandSoldering
FB12 | FILTER | w_smd_inductors:inductor_smd_0805
FI4 | NFE61P | DriveParts:EMI_Filter_murata
I5 | DS90LV028A | Housings_SOIC:SOIC-8_3.9x4.9mm_Pitch1.27mm
R21 | 240 | Resistors_SMD:R_0603_HandSoldering
R20 | 240 | Resistors_SMD:R_0603_HandSoldering
C57 | 100n | Capacitors_SMD:C_0603_HandSoldering
P10 | GATE_IO_A | Connectors:IDC_Header_Straight_16pins
R52 | 0 | Resistors_SMD:R_0603_HandSoldering
FB13 | FILTER | w_smd_inductors:inductor_smd_0805
C62 | 10u | Capacitors_SMD:C_0805
I6 | DS90LV028A | Housings_SOIC:SOIC-8_3.9x4.9mm_Pitch1.27mm
R23 | 240 | Resistors_SMD:R_0603_HandSoldering
R22 | 240 | Resistors_SMD:R_0603_HandSoldering
C58 | 100n | Capacitors_SMD:C_0603_HandSoldering
P11 | GATE_IO_A | Connectors:IDC_Header_Straight_16pins
R35 | 10k | Resistors_SMD:R_0603_HandSoldering
U8 | LM339 | Housings_SOIC:SOIC-14_3.9x8.7mm_Pitch1.27mm
R53 | 0 | Resistors_SMD:R_0603_HandSoldering
FB14 | FILTER | w_smd_inductors:inductor_smd_0805
CN7 | CONN_02X10 | Socket_Strips:Socket_Strip_Straight_2x10_Pitch2.54mm
CN10 | CONN_02X17 | Socket_Strips:Socket_Strip_Straight_2x17_Pitch2.54mm
CN8 | CONN_02X08 | Socket_Strips:Socket_Strip_Straight_2x08_Pitch2.54mm
CN9 | CONN_02X15 | Socket_Strips:Socket_Strip_Straight_2x15_Pitch2.54mm
D5 | 3.3V | Diodes_SMD:D_SOD-523
C61 | 10u | Capacitors_SMD:C_0805
R34 | 10k | Resistors_SMD:R_0603_HandSoldering
D4 | 3.3V | Diodes_SMD:D_SOD-523
C60 | 10u | Capacitors_SMD:C_0805
R33 | 10k | Resistors_SMD:R_0603_HandSoldering
C67 | 100n | Capacitors_SMD:C_0603_HandSoldering
D3 | 3.3V | Diodes_SMD:D_SOD-523
C64 | 100n | Capacitors_SMD:C_0603_HandSoldering
R4 | ? | Resistors_SMD:R_0603_HandSoldering
C25 | 1u | Capacitors_SMD:C_0603_HandSoldering
R3 | ? | Resistors_SMD:R_0603_HandSoldering
C72 | 1n | Capacitors_SMD:C_0603_HandSoldering
L16 | 1uH | w_smd_inductors:inductor_smd_0603
C70 | 10u | Capacitors_SMD:C_0805
R16 | DNP | Resistors_SMD:R_0603_HandSoldering
R17 | DNP | Resistors_SMD:R_0603_HandSoldering
R15 | DNP | Resistors_SMD:R_0603_HandSoldering
R14 | 240 | Resistors_SMD:R_0603_HandSoldering
C54 | 4u7 | Capacitors_SMD:C_0805
C51 | 100n | Capacitors_SMD:C_0603_HandSoldering
D1 | SP0503BAHT | TO_SOT_Packages_SMD:SOT-143 | http://www.littelfuse.com/~/media/files/littelfuse/technical%20resources/documents/data%20sheets/sp05xxba.pdf
C82 | 100n | Capacitors_SMD:C_0603_HandSoldering
P9 | GATE_IO_A | Connectors:IDC_Header_Straight_16pins
U3 | MCP101-315D | TO_SOT_Packages_SMD:SOT-23_Handsoldering | http://ww1.microchip.com/downloads/en/DeviceDoc/11187f.pdf
C83 | 100n | Capacitors_SMD:C_0603_HandSoldering
C78 | 47n | Capacitors_SMD:C_0603_HandSoldering
R12 | DNP | Resistors_SMD:R_0603_HandSoldering
R57 | DNP | Resistors_SMD:R_0603_HandSoldering
C77 | 47n | Capacitors_SMD:C_0603_HandSoldering
R59 | 0R | Resistors_SMD:R_0603_HandSoldering
R58 | DNP | Resistors_SMD:R_0603_HandSoldering
R11 | DNP | Resistors_SMD:R_0603_HandSoldering
R9 | DNP | Resistors_SMD:R_0603_HandSoldering
D2 | 3.3V | Diodes_SMD:D_SOD-523
FI5 | NFE61P | DriveParts:EMI_Filter_murata
U7 | OPA2340 | Housings_SOIC:SOIC-8_3.9x4.9mm_Pitch1.27mm | http://www.ti.com/lit/ds/symlink/opa4340.pdf
J13 | Regen | DriveParts:Test_Point
J8 | 12V | DriveParts:Test_Point
J12 | 5V | DriveParts:Test_Point
J10 | GND | DriveParts:Test_Point
J9 | GND | DriveParts:Test_Point
J11 | GND | DriveParts:Test_Point
D14 | Led_Small | LEDs:LED_0603_HandSoldering
D15 | Led_Small | LEDs:LED_0603_HandSoldering
D16 | Led_Small | LEDs:LED_0603_HandSoldering
D11 | ~PWM1 | LEDs:LED_0603_HandSoldering
R63 | 100 | LEDs:LED_0603_HandSoldering
D8 | PWM1 | LEDs:LED_0603_HandSoldering
R60 | 100 | LEDs:LED_0603_HandSoldering
J15 | PWM1 | DriveParts:Test_Point
J18 | ~PWM1 | DriveParts:Test_Point
I8 | DS90LV027A | Housings_SOIC:SOIC-8_3.9x4.9mm_Pitch1.27mm
C87 | 100n | Capacitors_SMD:C_0603_HandSoldering
D12 | ~PWM2 | LEDs:LED_0603_HandSoldering
R64 | 100 | LEDs:LED_0603_HandSoldering
D9 | PWM2 | LEDs:LED_0603_HandSoldering
R61 | 100 | LEDs:LED_0603_HandSoldering
J16 | PWM2 | DriveParts:Test_Point
J19 | ~PWM2 | DriveParts:Test_Point
I9 | DS90LV027A | Housings_SOIC:SOIC-8_3.9x4.9mm_Pitch1.27mm
C88 | 100n | Capacitors_SMD:C_0603_HandSoldering
D13 | ~PWM3 | LEDs:LED_0603_HandSoldering
R65 | 100 | LEDs:LED_0603_HandSoldering
D10 | PWM3 | LEDs:LED_0603_HandSoldering
R62 | 100 | LEDs:LED_0603_HandSoldering
J17 | PWM3 | DriveParts:Test_Point
J20 | ~PWM3 | DriveParts:Test_Point
J14 | Throttle | DriveParts:Test_Point
J2 | QSPI_CLK | DriveParts:Test_Point
J3 | QSPI_NCS | DriveParts:Test_Point
J4 | QSPI_IO0 | DriveParts:Test_Point
J5 | QSPI_IO1 | DriveParts:Test_Point
J6 | QSPI_IO2 | DriveParts:Test_Point
J7 | QSPI_IO3 | DriveParts:Test_Point
J25 | Overtemp | DriveParts:Test_Point
J21 | OCV | DriveParts:Test_Point
J26 | PWM1 | DriveParts:Test_Point
J22 | ~F_C | DriveParts:Test_Point
J23 | ~F_B | DriveParts:Test_Point
J24 | ~F_A | DriveParts:Test_Point
J27 | Conn_01x04_Female | Connectors_Terminal_Blocks:TerminalBlock_Pheonix_PT-3.5mm_4pol
L9 | 10uH | Inductors_NEOSID:Neosid_Inductor_SM-NE30_SMD1210
C84 | 10u, 6.3v | Capacitors_SMD:C_0805
L18 | 10uH | Inductors_NEOSID:Neosid_Inductor_SM-NE30_SMD1210
C85 | 10u, 6.3v | Capacitors_SMD:C_0805
R66 | 0 | Resistors_SMD:R_0603_HandSoldering
J29 | Conn_01x04 | Connectors_Phoenix:PhoenixContact_MSTB-GF_04x5.08mm_Angled_ThreadedFlange_MountHole
R67 | 10k | Resistors_SMD:R_0603_HandSoldering
J30 | SPI2_SCK | DriveParts:Test_Point
J31 | SPI2_NSS | DriveParts:Test_Point
J32 | SPI2_MOSI | DriveParts:Test_Point
J33 | SPI2_MISO | DriveParts:Test_Point
J35 | 3V3 | DriveParts:Test_Point
J34 | PS-DIS | DriveParts:Test_Point
J36 | GND | DriveParts:Test_Point
J37 | GND | DriveParts:Test_Point
U1 | LM1117-5.0 | TO_SOT_Packages_SMD:TO-263-3_TabPin2 | http://www.ti.com/lit/ds/symlink/lm1117.pdf
U2 | LM1117-3.3 | TO_SOT_Packages_SMD:TO-263-3_TabPin2 | http://www.ti.com/lit/ds/symlink/lm1117.pdf
FL1 | Wurth_744273501 | DriveParts:WE_SL5_HR_CommonMode_filter
U11 | FT232RL | Housings_SSOP:SSOP-28_5.3x10.2mm_Pitch0.65mm | http://www.ftdichip.com/Products/ICs/FT232RL.htm
L1 | BLM18PG121SN1D | w_smd_inductors:inductor_smd_0603
C10 | 10n | Capacitors_SMD:C_0603_HandSoldering
C24 | 100n | Capacitors_SMD:C_0603_HandSoldering
R55 | 240 | Resistors_SMD:R_0603_HandSoldering
D18 | RX | LEDs:LED_0603_HandSoldering
D17 | TX | LEDs:LED_0603_HandSoldering
J1 | USB_OTG | Connectors:USB_Mini-B
MK2 | Mounting_Hole_PAD | Mounting_Holes:MountingHole_4.3mm_M4_Pad_Via
MK3 | Mounting_Hole_PAD | Mounting_Holes:MountingHole_4.3mm_M4_Pad_Via
MK4 | Mounting_Hole_PAD | Mounting_Holes:MountingHole_4.3mm_M4_Pad_Via
MK1 | Mounting_Hole_PAD | Mounting_Holes:MountingHole_4.3mm_M4_Pad_Via
MK5 | Mounting_Hole | Mounting_Holes:MountingHole_3.2mm_M3
MK6 | Mounting_Hole | Mounting_Holes:MountingHole_3.2mm_M3
MK7 | Mounting_Hole | Mounting_Holes:MountingHole_3.2mm_M3
MK8 | Mounting_Hole | Mounting_Holes:MountingHole_3.2mm_M3
MK9 | Mounting_Hole | Mounting_Holes:MountingHole_3.2mm_M3
J38 | AGND | DriveParts:Test_Point
J39 | SP1_MISO | DriveParts:Test_Point
J40 | SP1_SCK | DriveParts:Test_Point
J41 | SP1_NSS | DriveParts:Test_Point
J42 | SP1_MOSI | DriveParts:Test_Point
J43 | DB15_Female_HighDensity_MountingHoles | DriveParts:DB_15F-VGA-mountingholes

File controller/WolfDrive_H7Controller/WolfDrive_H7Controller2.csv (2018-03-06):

Qty | partname | description | lib
0 | Power_Management:MCP101-315D |  | WolfDrive_H7Controller-cache
0 | WolfDrive_H7Controller-rescue:ESD_Protection_SP0503BAHT-RESCUE-WolfDrive_H7Controller |  | WolfDrive_H7Controller-cache
0 | WolfDrive_H7Controller-rescue:WolfDrive_H7Controller-rescue_74LS136-RESCUE-WolfDrive_H7Controller |  | WolfDrive_H7Controller-cache
0 | WolfDrive_H7Controller-rescue:WolfDrive_H7Controller-rescue_AFBR-1634Z-RESCUE-WolfDrive_H7Controller |  | WolfDrive_H7Controller-cache
0 | WolfDrive_H7Controller-rescue:WolfDrive_H7Controller-rescue_AFBR-26x-RESCUE-WolfDrive_H7Controller |  | WolfDrive_H7Controller-cache
0 | WolfDrive_H7Controller-rescue:WolfDrive_H7Controller-rescue_CD4044B-RESCUE-WolfDrive_H7Controller |  | WolfDrive_H7Controller-cache
0 | WolfDrive_H7Controller-rescue:WolfDrive_H7Controller-rescue_CONN_01X02-RESCUE-WolfDrive_H7Controller |  | WolfDrive_H7Controller-cache
0 | WolfDrive_H7Controller-rescue:WolfDrive_H7Controller-rescue_CONN_02X08-RESCUE-WolfDrive_H7Controller |  | WolfDrive_H7Controller-cache
0 | WolfDrive_H7Controller-rescue:WolfDrive_H7Controller-rescue_CONN_02X10-RESCUE-WolfDrive_H7Controller |  | WolfDrive_H7Controller-cache
0 | WolfDrive_H7Controller-rescue:WolfDrive_H7Controller-rescue_CONN_02X15-RESCUE-WolfDrive_H7Controller |  | WolfDrive_H7Controller-cache
0 | WolfDrive_H7Controller-rescue:WolfDrive_H7Controller-rescue_CONN_02X17-RESCUE-WolfDrive_H7Controller |  | WolfDrive_H7Controller-cache
0 | WolfDrive_H7Controller-rescue:WolfDrive_H7Controller-rescue_DS90LV027A-RESCUE-WolfDrive_H7Controller |  | WolfDrive_H7Controller-cache
0 | WolfDrive_H7Controller-rescue:WolfDrive_H7Controller-rescue_DS9637A-RESCUE-WolfDrive_H7Controller |  | WolfDrive_H7Controller-cache
0 | WolfDrive_H7Controller-rescue:WolfDrive_H7Controller-rescue_EMI_FILTER-RESCUE-WolfDrive_H7Controller |  | WolfDrive_H7Controller-cache
0 | WolfDrive_H7Controller-rescue:WolfDrive_H7Controller-rescue_FILTER-RESCUE-WolfDrive_H7Controller |  | WolfDrive_H7Controller-cache
0 | WolfDrive_H7Controller-rescue:WolfDrive_H7Controller-rescue_INDUCTOR_SMALL-RESCUE-WolfDrive_H7Controller |  | WolfDrive_H7Controller-cache
0 | WolfDrive_H7Controller-rescue:WolfDrive_H7Controller-rescue_LTV-356T-RESCUE-WolfDrive_H7Controller |  | WolfDrive_H7Controller-cache
0 | WolfDrive_H7Controller-rescue:WolfDrive_H7Controller-rescue_Led_Small-RESCUE-WolfDrive_H7Controller |  | WolfDrive_H7Controller-cache
0 | WolfDrive_H7Controller-rescue:WolfDrive_H7Controller-rescue_ZENER-RESCUE-WolfDrive_H7Controller |  | WolfDrive_H7Controller-cache
0 | WolfDrive_H7Controller-rescue:conn_SD_Card-RESCUE-WolfDrive_H7Controller |  | WolfDrive_H7Controller-cache
0 | WolfDrive_H7Controller-rescue:device_C-RESCUE-WolfDrive_H7Controller |  | WolfDrive_H7Controller-cache
0 | WolfDrive_H7Controller-rescue:device_Q_NMOS_DGS-RESCUE-WolfDrive_H7Controller |  | WolfDrive_H7Controller-cache
0 | WolfDrive_H7Controller-rescue:device_R-RESCUE-WolfDrive_H7Controller |  | WolfDrive_H7Controller-cache
0 | WolfDrive_H7Controller-rescue:interface_ADuM1201CR-RESCUE-WolfDrive_H7Controller |  | WolfDrive_H7Controller-cache
0 | WolfDrive_H7Controller-rescue:linear_LM339-RESCUE-WolfDrive_H7Controller |  | WolfDrive_H7Controller-cache
0 | conn:Conn_01x04 |  | WolfDrive_H7Controller-cache
0 | conn:Conn_01x04_Female |  | WolfDrive_H7Controller-cache
0 | conn:DB15_Female_HighDensity_MountingHoles |  | WolfDrive_H7Controller-cache
0 | conn:TEST_1P |  | WolfDrive_H7Controller-cache
0 | conn:USB_OTG |  | WolfDrive_H7Controller-cache
0 | device:EMI_Filter_CommonMode |  | WolfDrive_H7Controller-cache
0 | device:Ferrite_Bead |  | WolfDrive_H7Controller-cache
0 | device:R_Small |  | WolfDrive_H7Controller-cache
0 | ftdi:FT232RL |  | WolfDrive_H7Controller-cache
0 | linear:OPA2340 |  | WolfDrive_H7Controller-cache
0 | mechanical:Mounting_Hole |  | WolfDrive_H7Controller-cache
0 | mechanical:Mounting_Hole_PAD |  | WolfDrive_H7Controller-cache
0 | regul:LM1117-3.3 |  | WolfDrive_H7Controller-cache
0 | regul:LM1117-5.0 |  | WolfDrive_H7Controller-cache

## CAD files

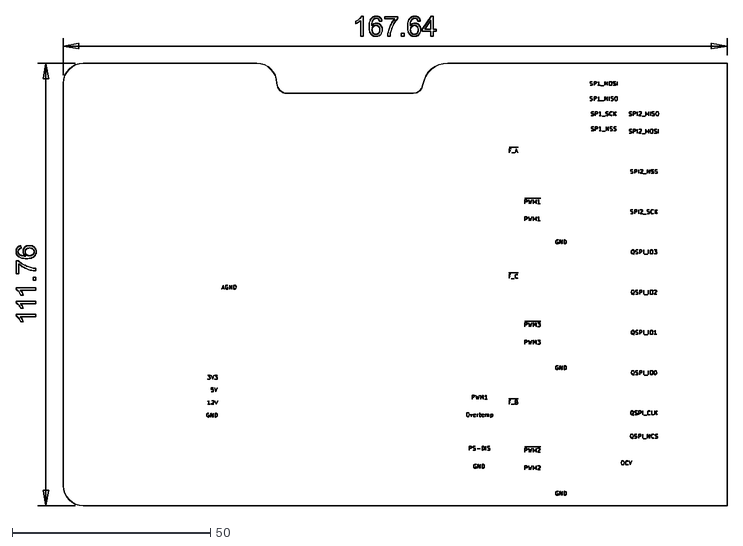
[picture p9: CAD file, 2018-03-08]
controller/WolfDrive_H7Controller/WolfDrive_H7Controller_fab/testpoint_labels.dxf
179.5 x 123.6

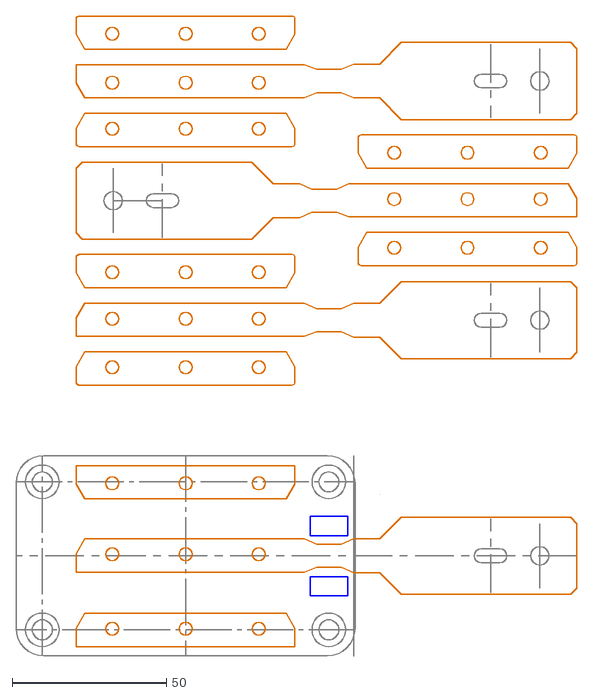
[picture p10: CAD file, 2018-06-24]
DCbus/drawings/Cree_CAS325_DC_Busbars.dxf
182.0 x 207.7

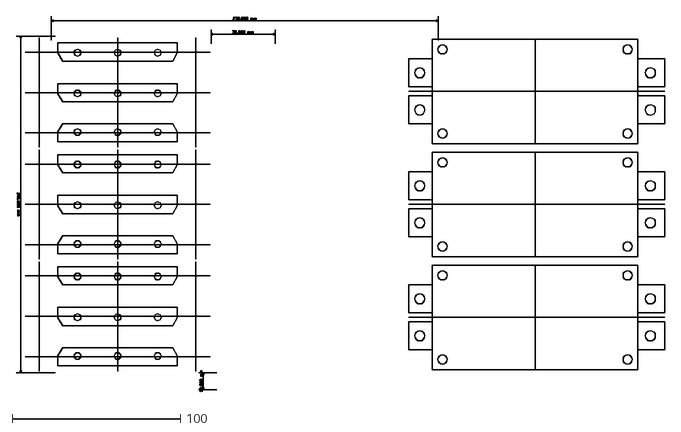
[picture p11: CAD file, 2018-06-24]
DCbus/WolfDrive_DCbus_fab/WolfDrive_DCbus-Dwgs.User.dxf
385.2 x 222.9

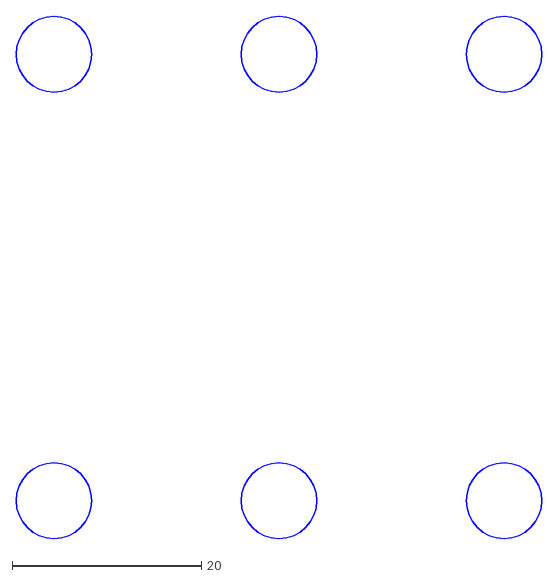
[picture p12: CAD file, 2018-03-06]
DCsnubber/drawings/Cree_CAS325_DCholes.dxf
55.6 x 55.2

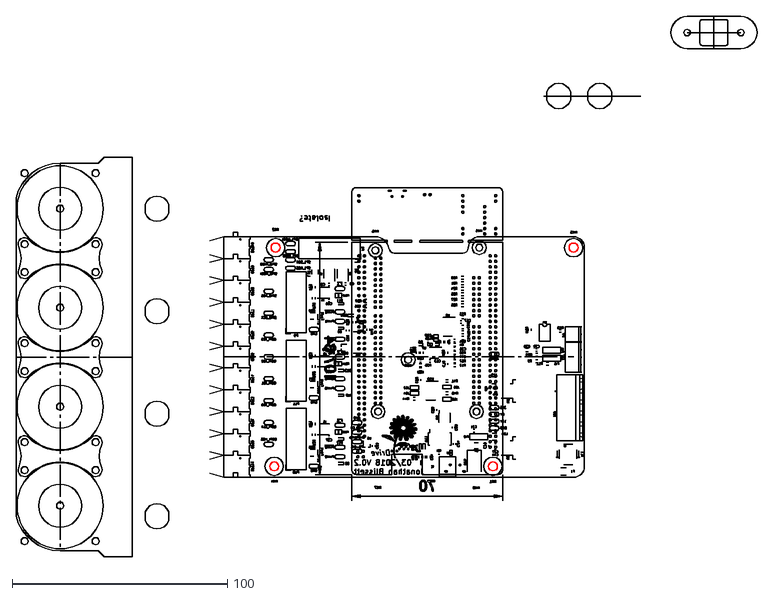
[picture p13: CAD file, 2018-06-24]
drawings/planview_top.dxf
344.3 x 251.0

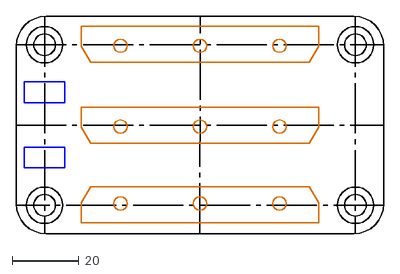
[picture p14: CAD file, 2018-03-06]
DCbus/drawings/Cree_CAS325_outline.dxf
110.0 x 65.0

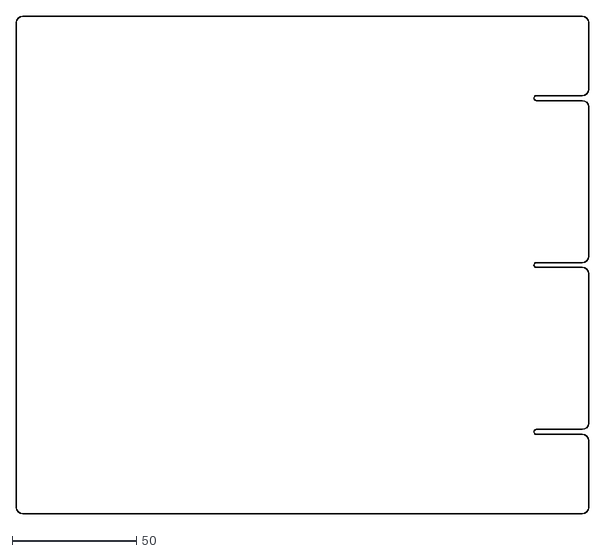
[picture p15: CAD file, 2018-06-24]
DCbus/WolfDrive_DCbus_fab/WolfDrive_DCbus-Edge.Cuts.dxf
230.0 x 200.0

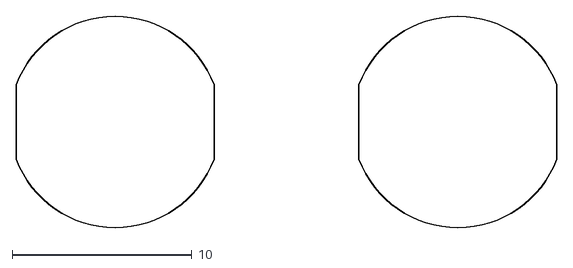
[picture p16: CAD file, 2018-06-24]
drawings/4mm_con_cutouts.dxf
30.1 x 11.8

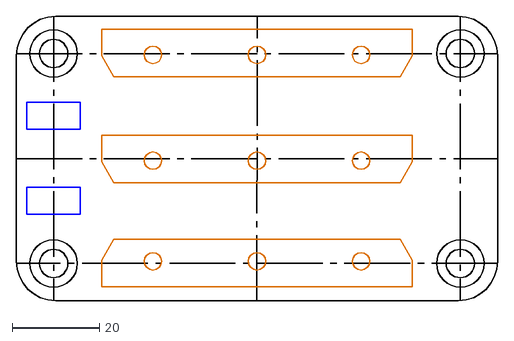
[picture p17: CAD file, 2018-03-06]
DCbus/drawings/Cree_CAS325_outline_DXF04.dxf
110.0 x 65.0

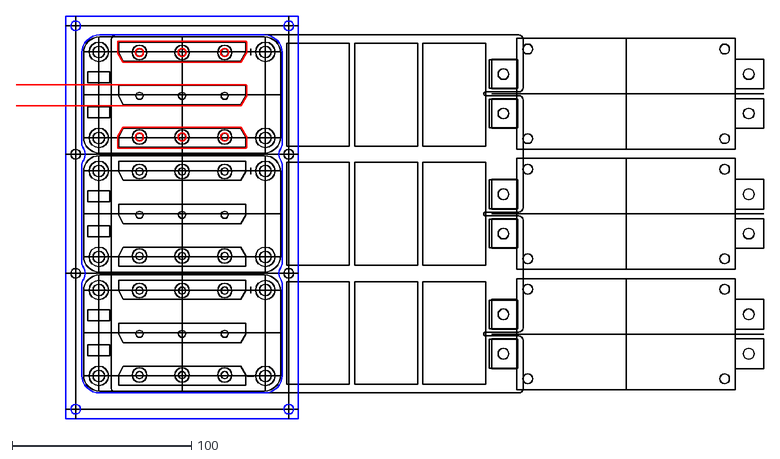
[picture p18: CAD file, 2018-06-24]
drawings/planview.dxf
417.7 x 225.0

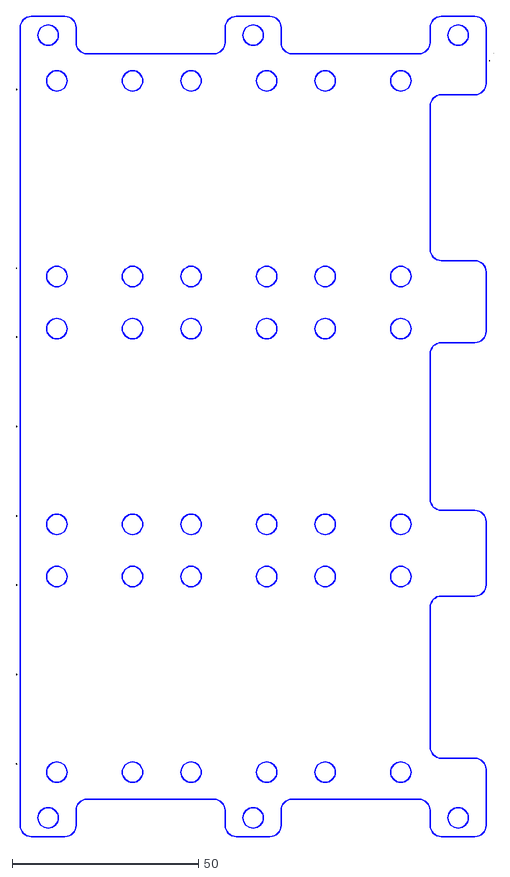
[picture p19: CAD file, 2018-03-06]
DCbus/drawings/wolf_support_only.dxf
128.0 x 220.0

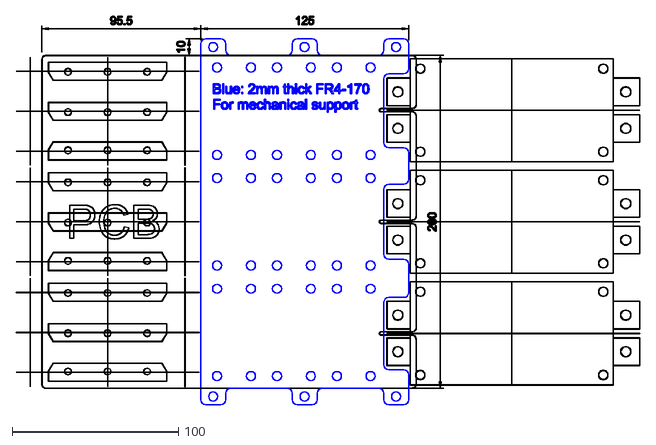
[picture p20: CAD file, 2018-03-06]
DCbus/drawings/wolf_support.dxf
375.1 x 233.6

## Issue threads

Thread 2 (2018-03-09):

Controller UART errors

jonblissett, 2018-03-09:
Pin 26 (TEST) on FT232RL should be connected to GND -> short to pin 25.
Device does not enumerate unless D1 (SP0503BAHT) is not populated.

Closed 2018-03-19.

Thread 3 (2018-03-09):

Controller schematic and PCB errors

jonblissett, 2018-03-09:
Protection diodes D1-D3 on over-temperature trips incorrect value and not required (DNP).
MOSFET Q2 footprint pinout incorrect.
CD4044B pinout incorrect - actually pinout for CD4043B so need to invert all fault inputs.
Footprint for DB15 vertical instead of right angle?
Connectors CN7-CNCN10 mirrored - connections to STM32 board do not match.

jonblissett, 2018-03-19:
Fixed in 41d57848ce190ba2b6ae11427ff5fd0c882f64ee

Closed 2018-03-19.

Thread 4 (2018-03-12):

Fault signal not triggered when gate driver is unplugged

jonblissett, 2018-03-12:
As per title. Maybe add weak pullup/down resistors to LVDS IC?

jonblissett, 2018-03-13:
Seems to be due to following comment in DS90LV028a datasheet:
"The receiver also supports open, shorted and terminated (100 Ω) input fail-safe. The receiver output is HIGH for all fail-safe conditions."

jonblissett, 2018-03-13:
Possible fix, swap FAULT differential pair pins from gate driver to invert signal. Fault will then be active high.

jonblissett, 2018-03-19:
Fixed by inverting FAULT differential pair in 41d57848ce190ba2b6ae11427ff5fd0c882f64ee

Closed 2018-03-19.

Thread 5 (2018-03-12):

Differential drivers have incorrect supply voltage

jonblissett, 2018-03-12:
DS90LV028A are rated for 3.3V supply, but schematic has 5V connected!

jonblissett, 2018-03-13:
Can use DS90C401 instead - 5V compatible part, but for new version use DS90LV027AQ-Q1 and supply with 3.3V.

Whole 5V supply may no longer be required?

jonblissett, 2018-03-19:
Fixed in 41d57848ce190ba2b6ae11427ff5fd0c882f64ee

Closed 2018-03-19.

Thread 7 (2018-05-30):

Incorrect PWM fault pin assignment

jonblissett, 2018-05-30:
Fault protection should be connected to PWM fault input, see datasheet #38.3.16 "Using the break function".

Temporary fix, use interrupt triggered software break?

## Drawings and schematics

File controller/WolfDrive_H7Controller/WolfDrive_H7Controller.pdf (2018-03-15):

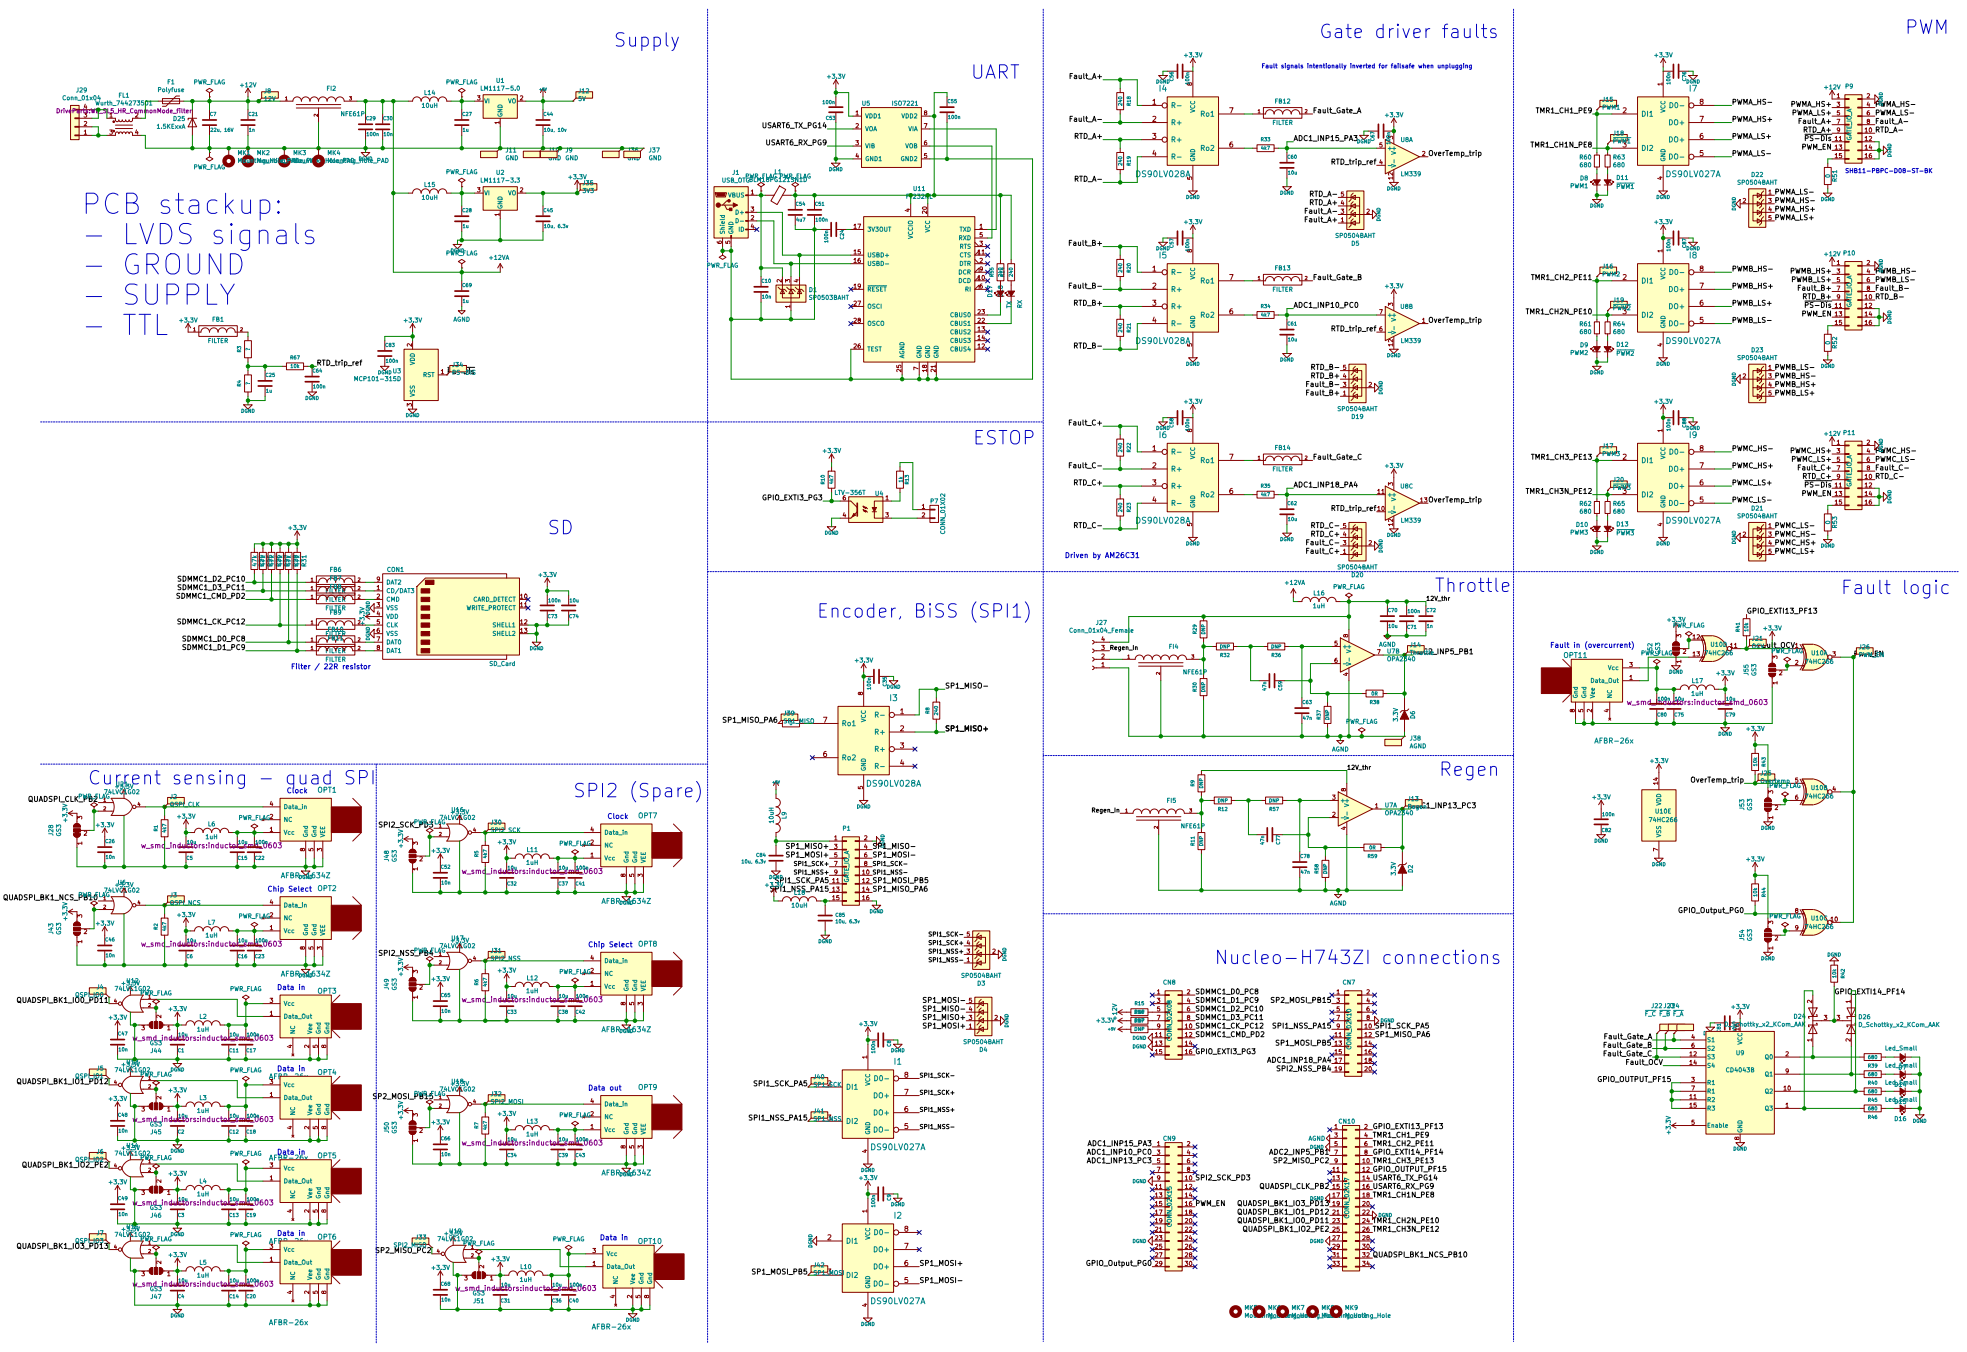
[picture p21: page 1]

Fault signals intentionally inverted for failsafe when unplugging

TXD 1 DCD 10 CTS 11 CBUS4 12 CBUS2 13 CBUS3 14 USBD+ 15 USBD- 16

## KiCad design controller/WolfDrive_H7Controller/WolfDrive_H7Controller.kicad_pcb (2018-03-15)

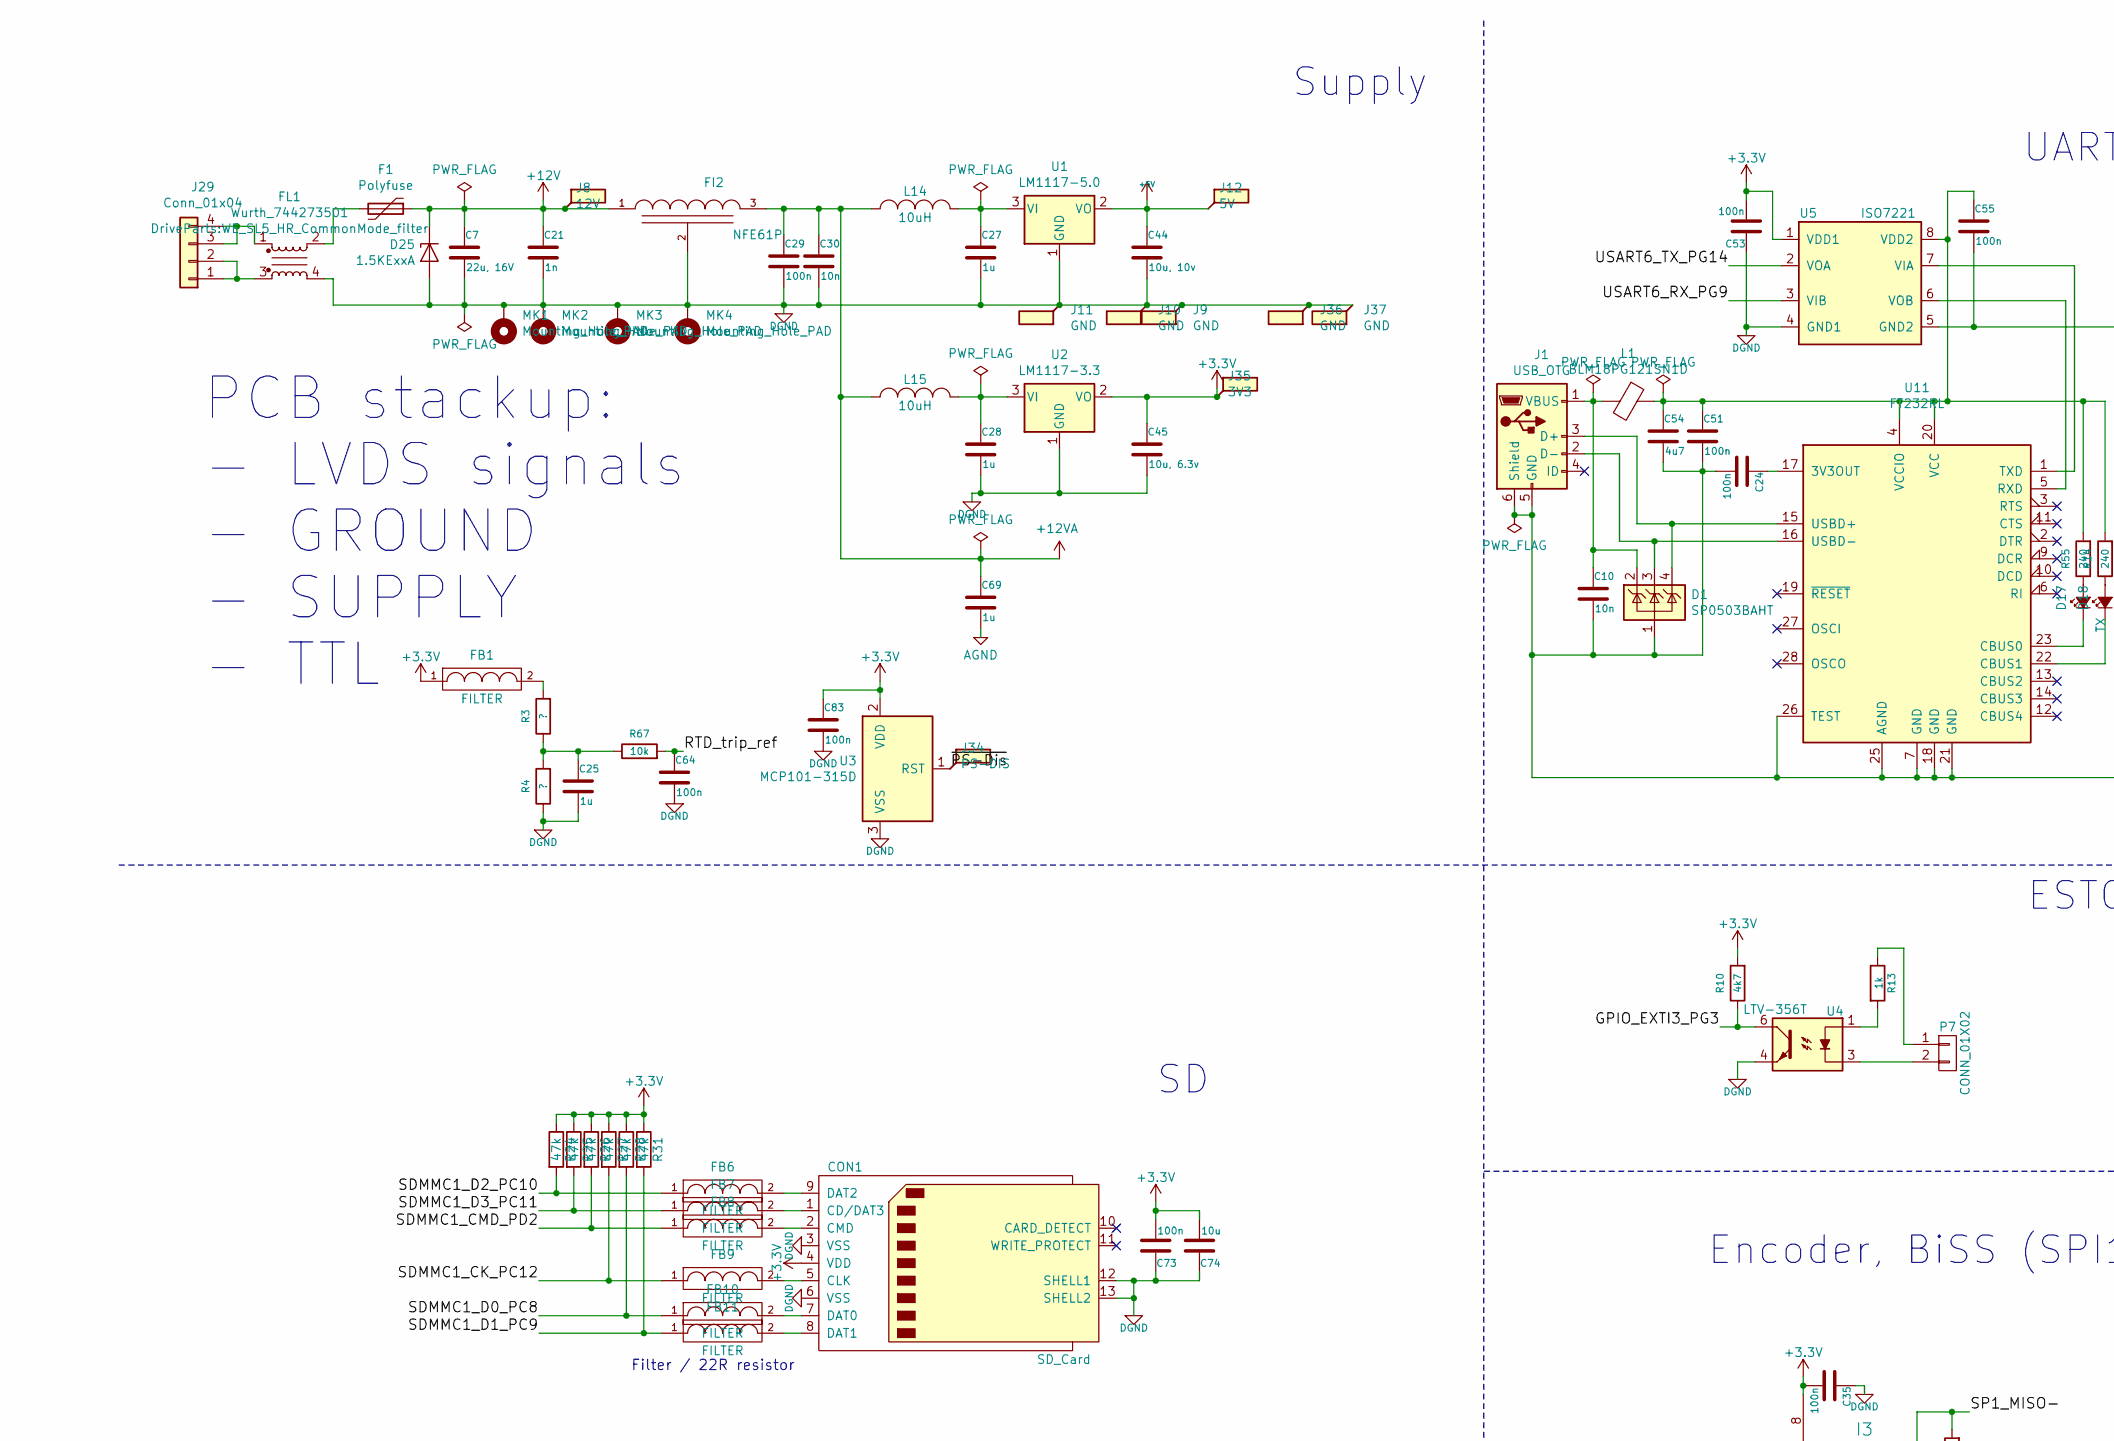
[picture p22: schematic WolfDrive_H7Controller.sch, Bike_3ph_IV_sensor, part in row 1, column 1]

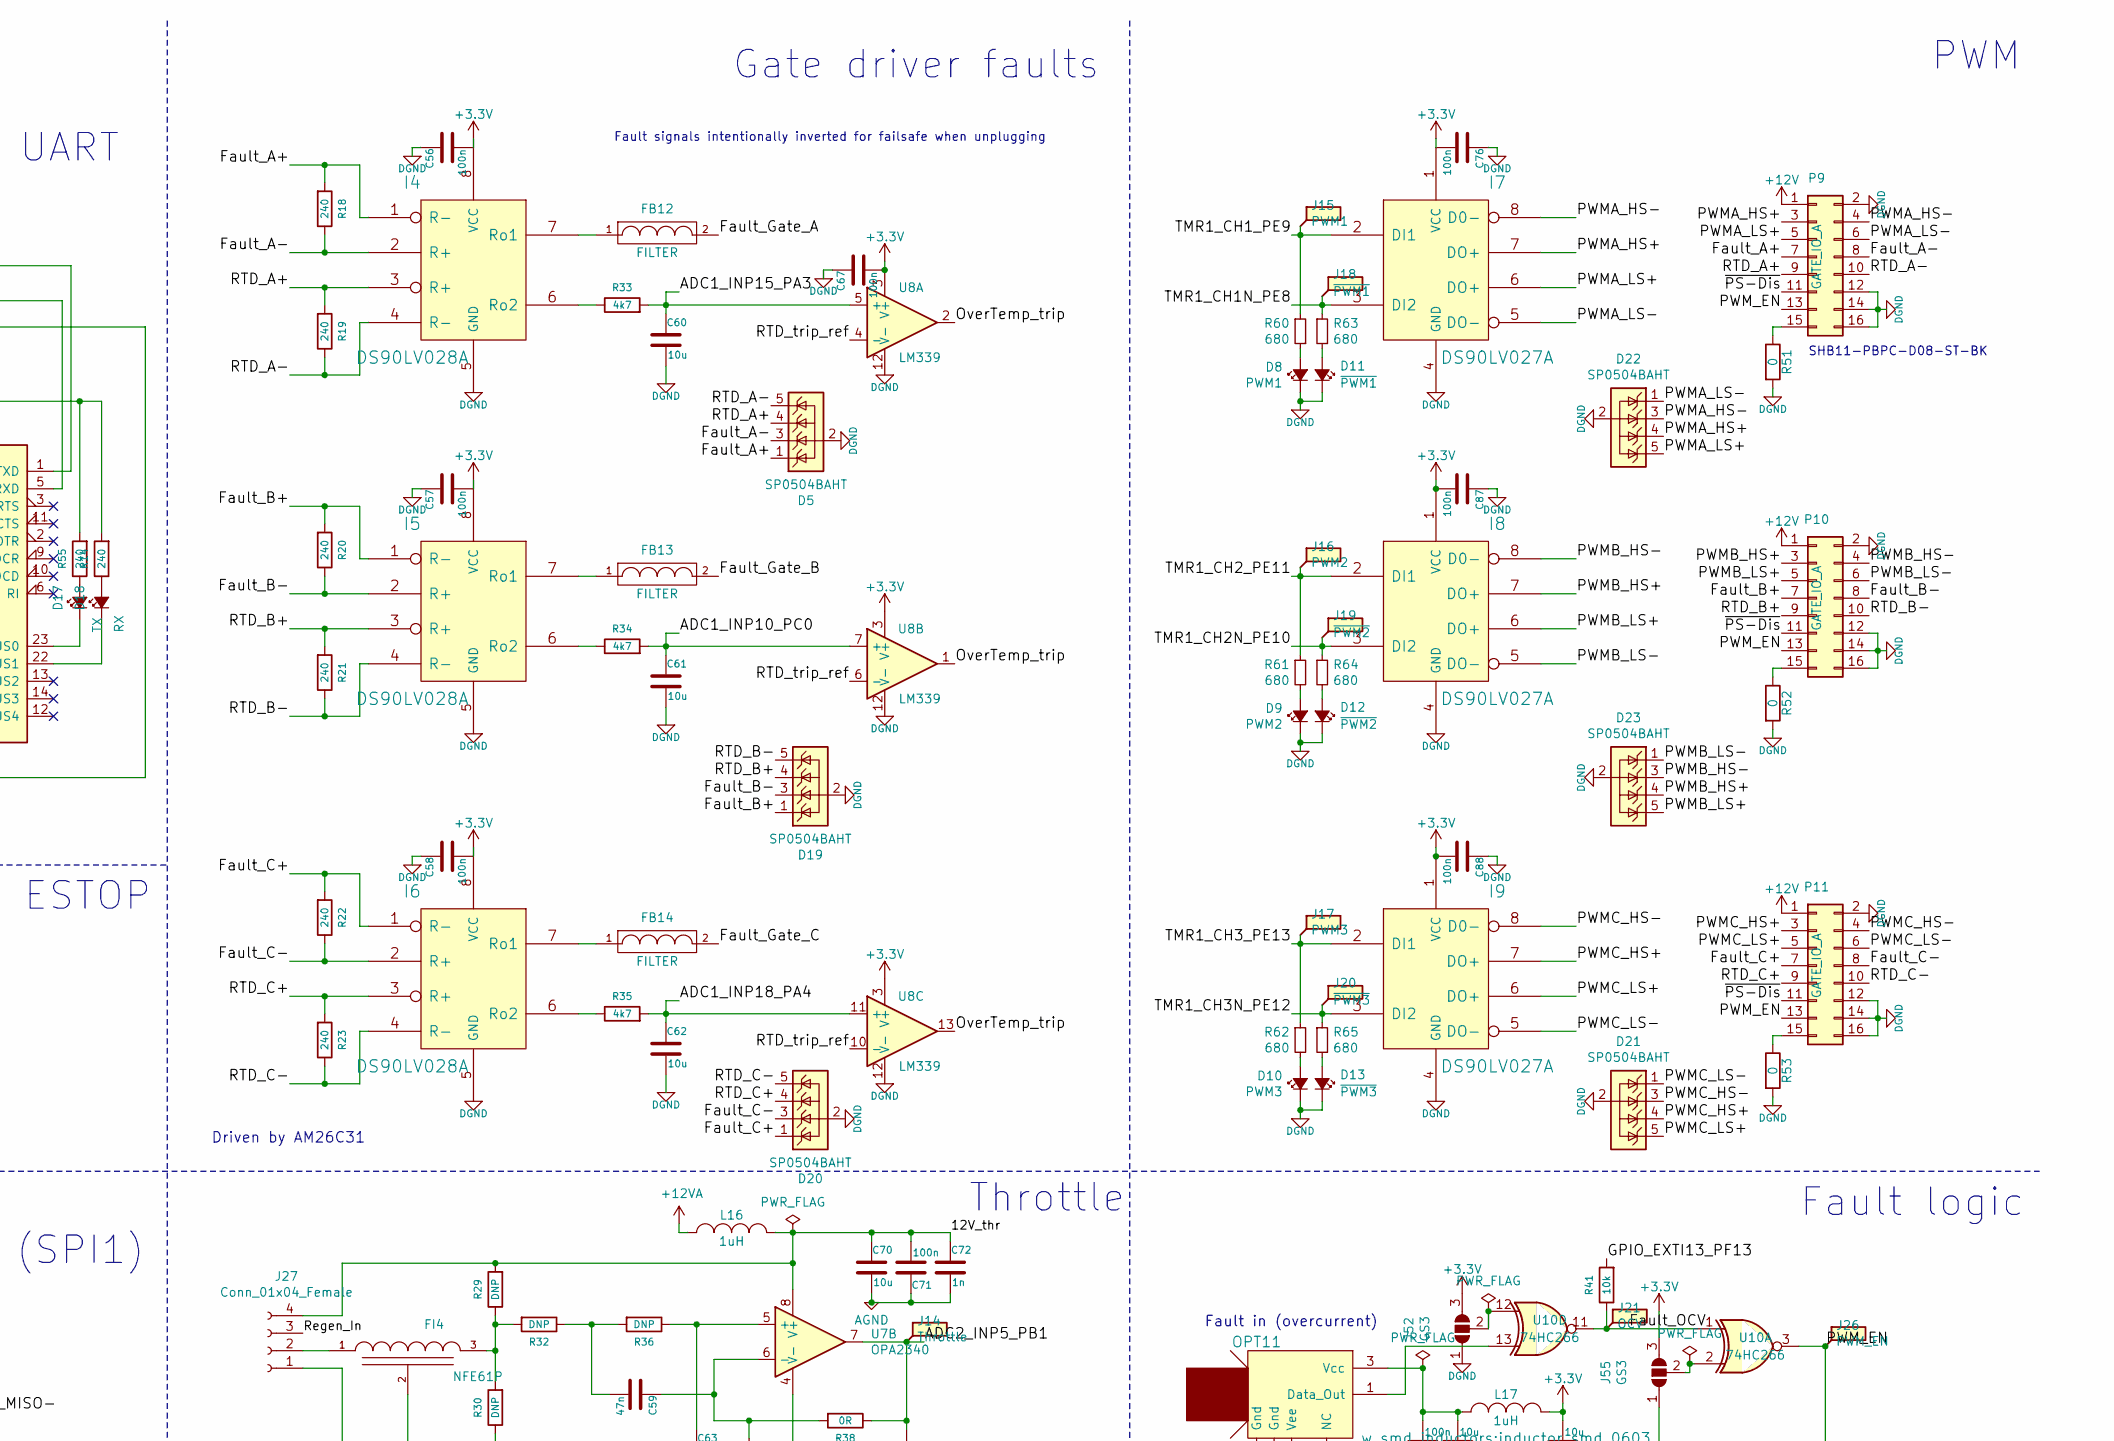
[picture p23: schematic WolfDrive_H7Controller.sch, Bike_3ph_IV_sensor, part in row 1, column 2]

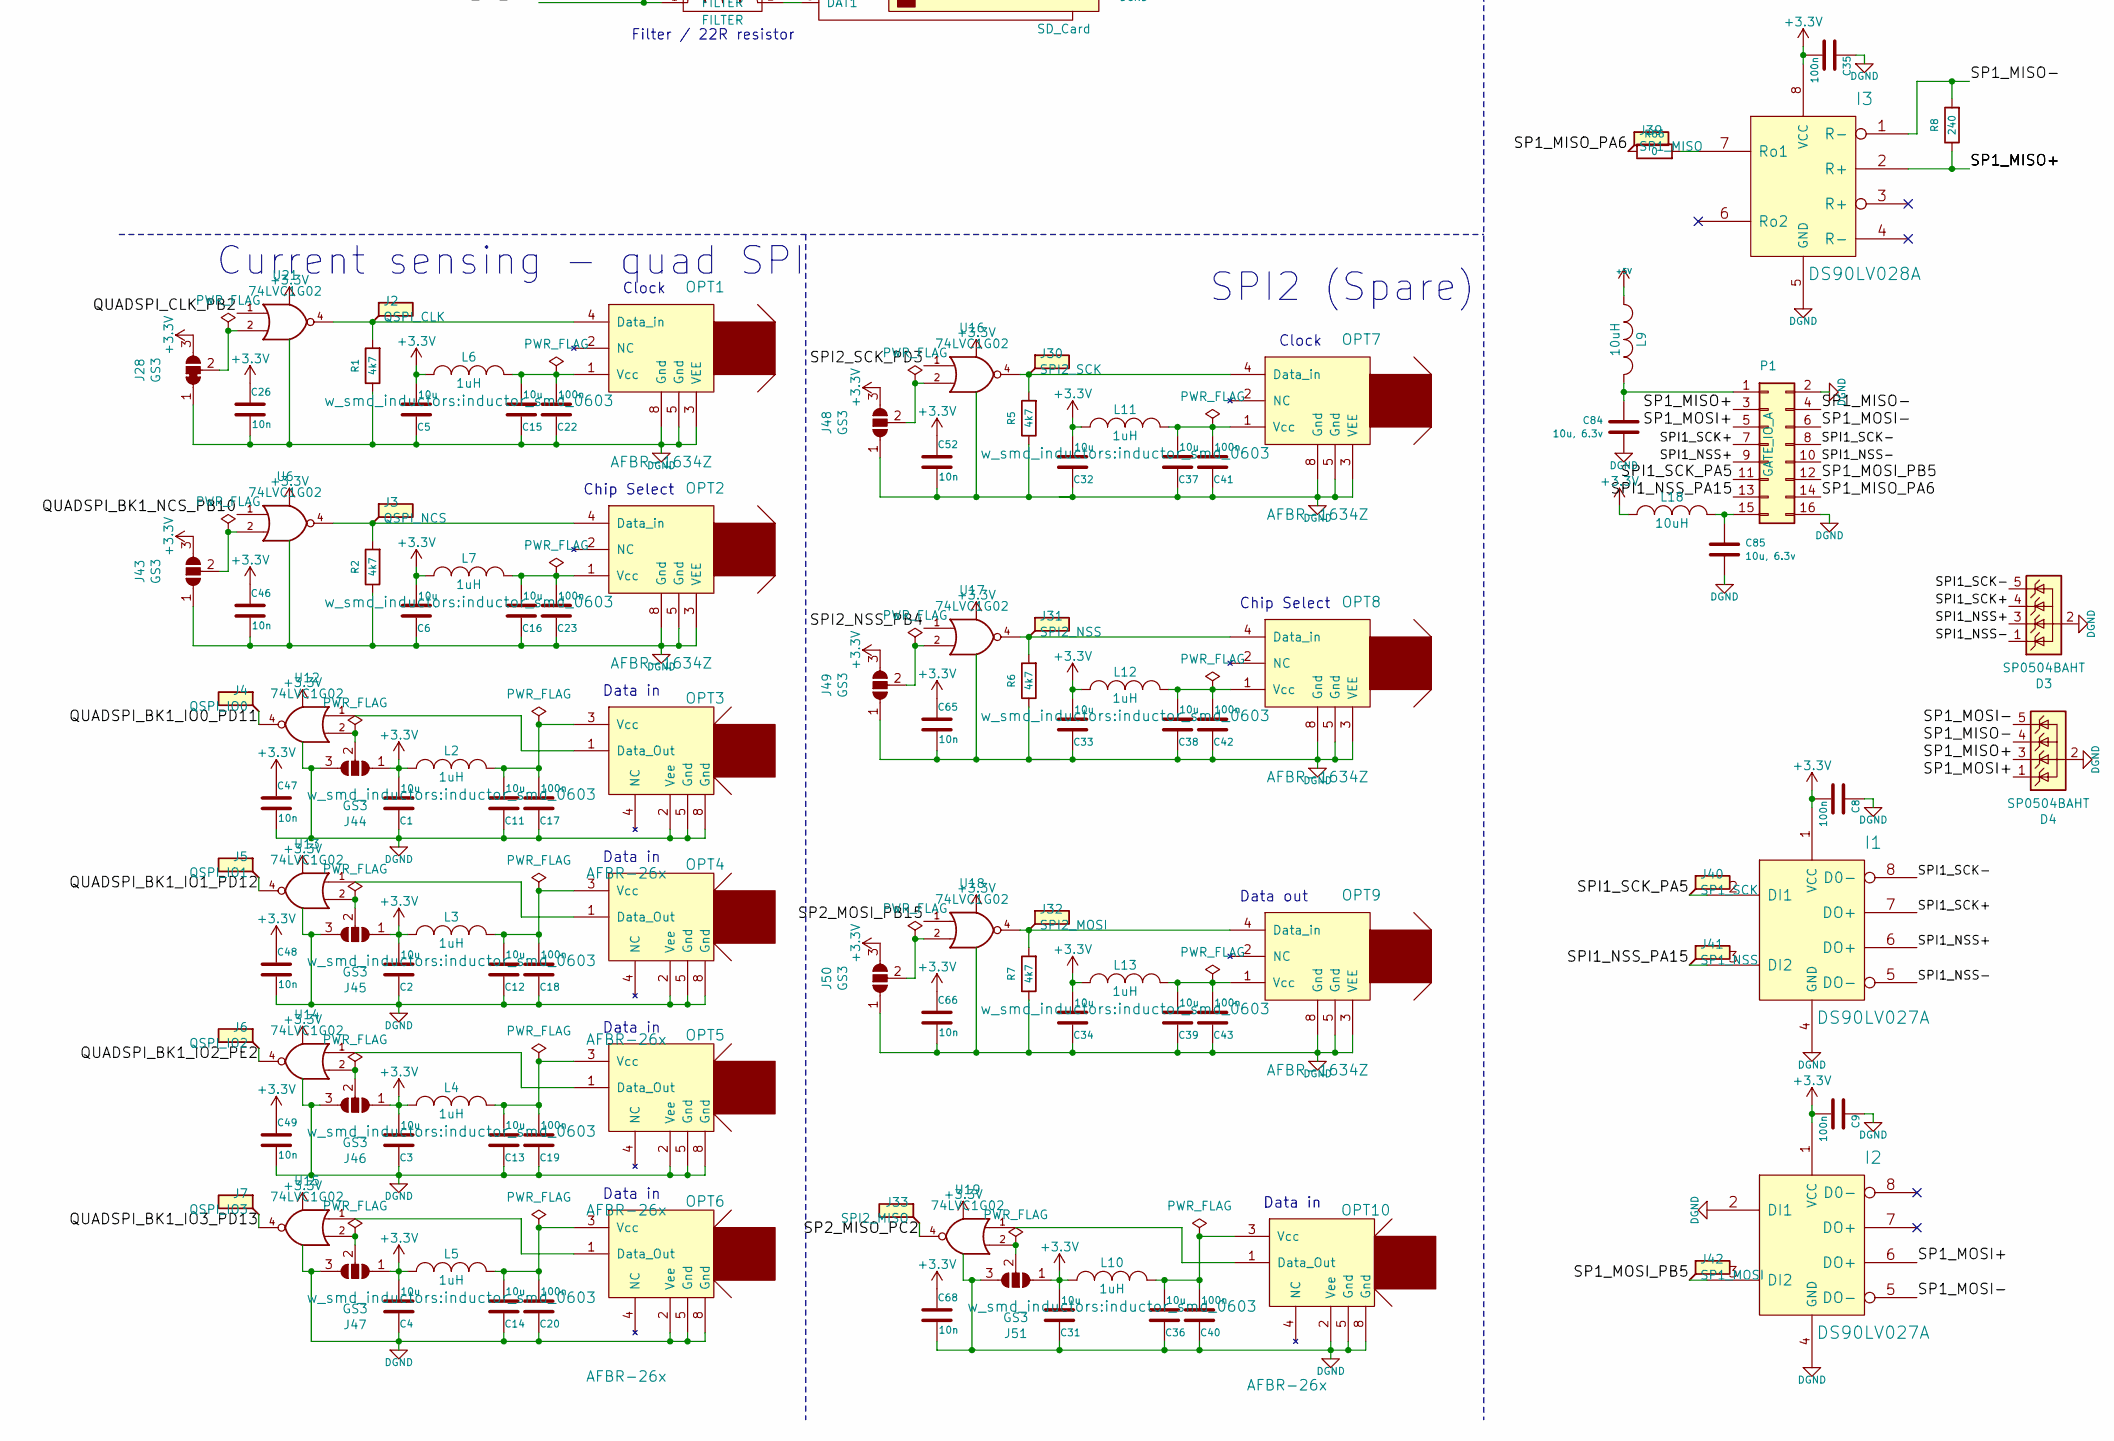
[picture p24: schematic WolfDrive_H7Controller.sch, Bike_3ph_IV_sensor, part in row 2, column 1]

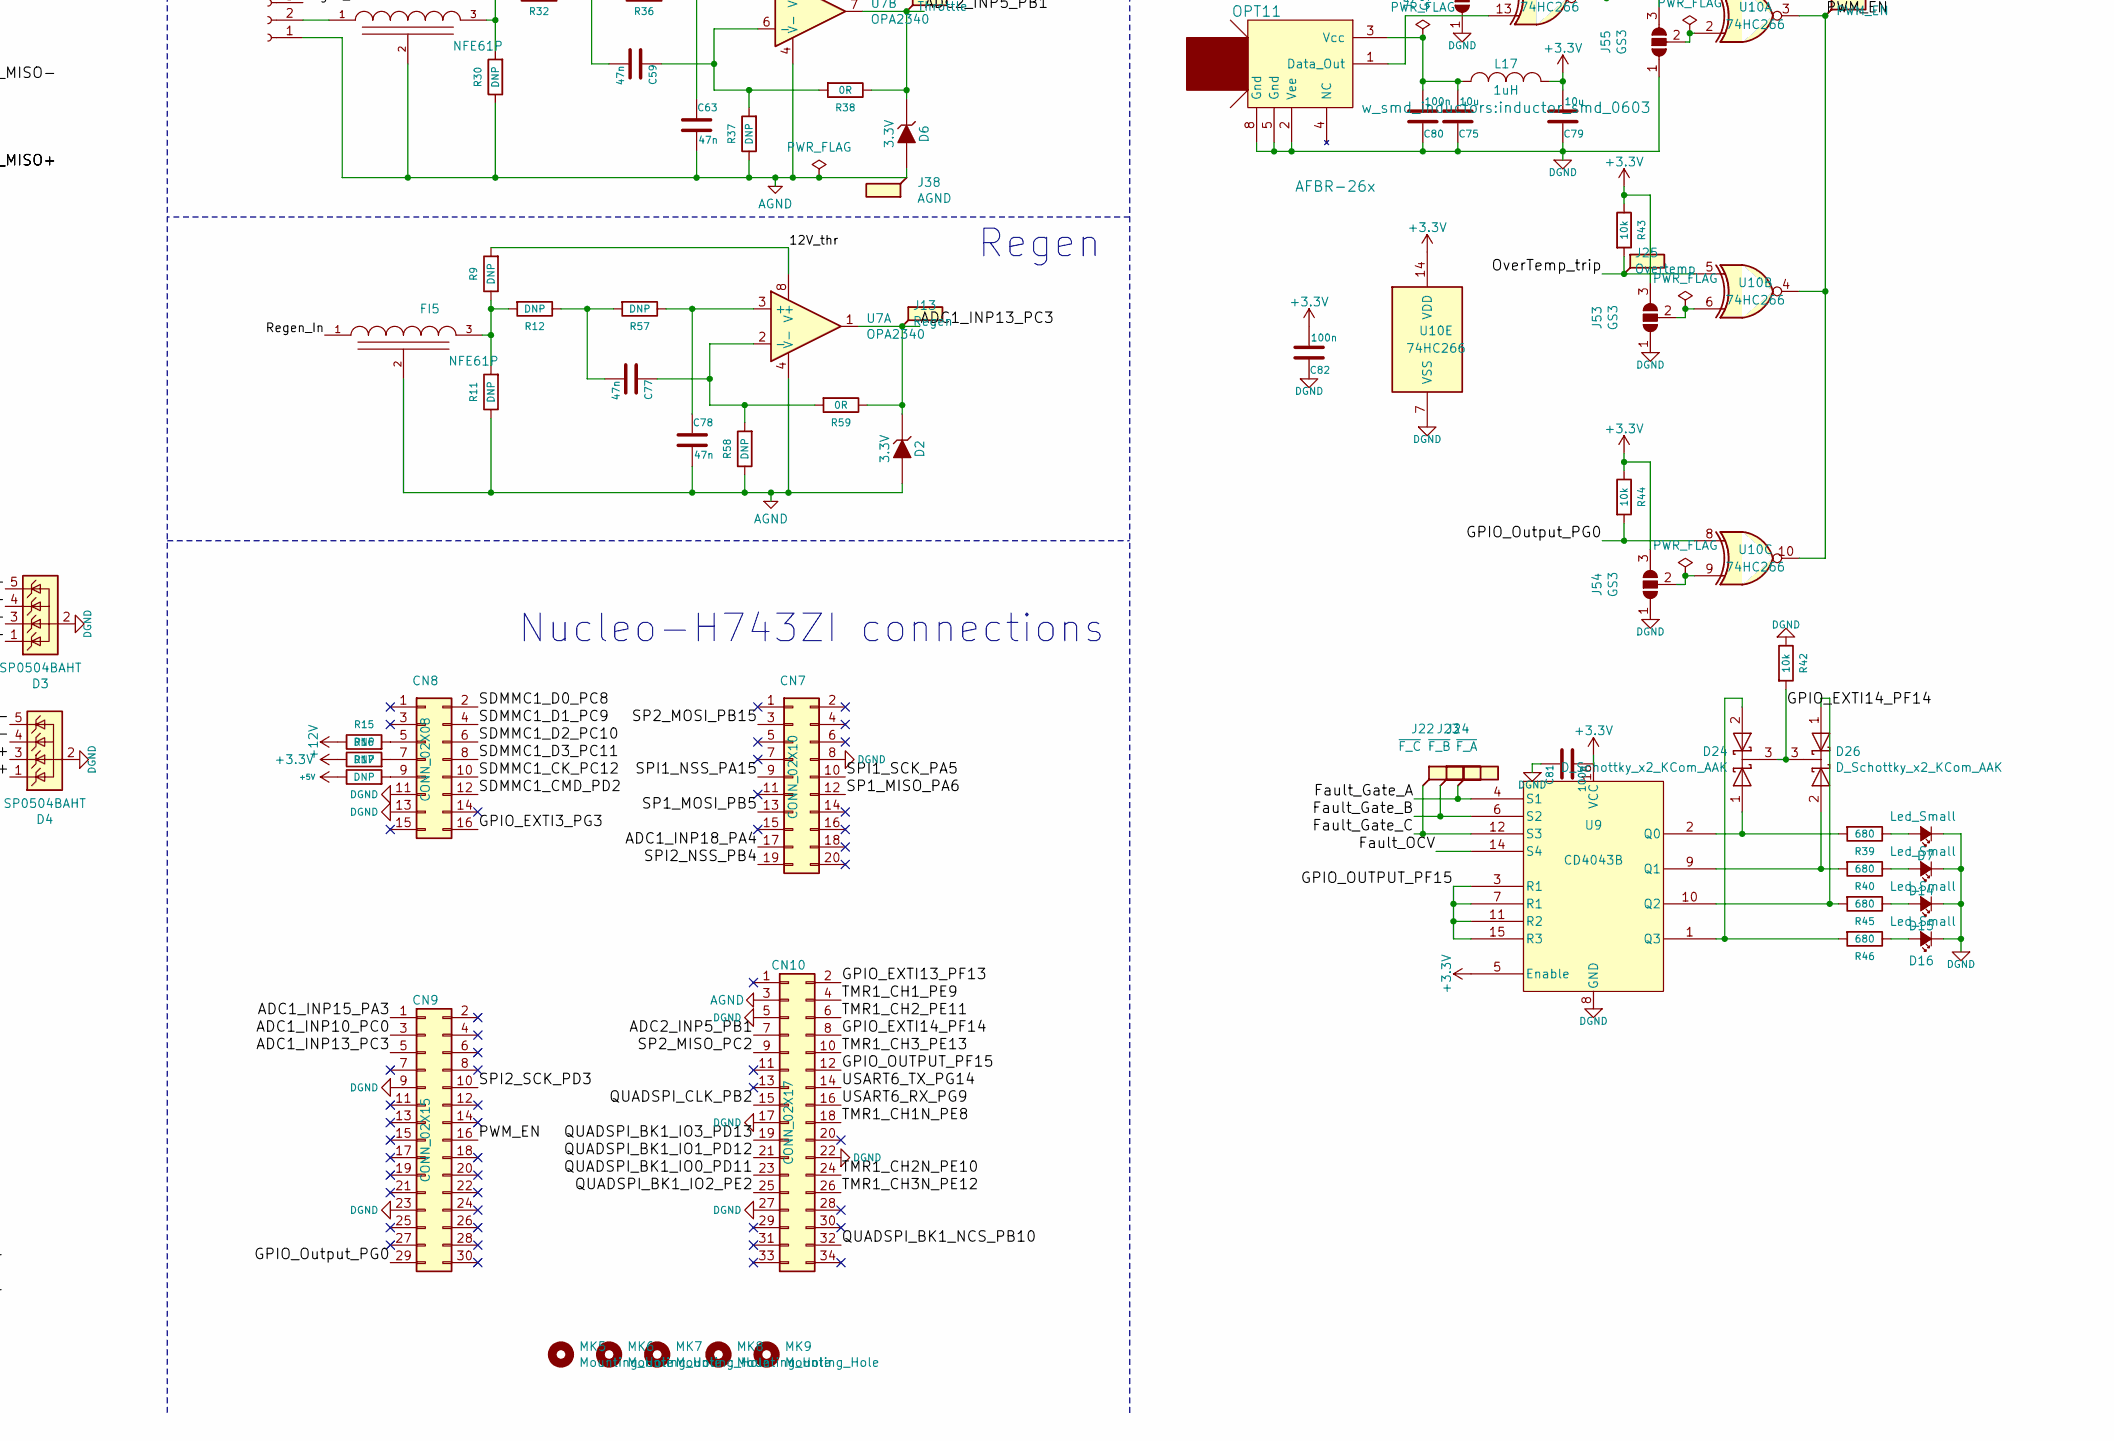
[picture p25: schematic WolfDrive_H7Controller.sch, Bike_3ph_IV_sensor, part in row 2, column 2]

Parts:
C1, C2, C3, C4, C5, C6, C11, C12, C13, C14, C15, C16, C31, C32, C33, C34, C36, C37, C38, C39, C60, C61, C62, C70, C74, C75, C79: 10u; C_0805
C7: 22u, 16V; C_1210_HandSoldering
C8, C9, C17, C18, C19, C20, C22, C23, C24, C29, C35, C40, C41, C42, C43, C51, C53, C55, C56, C57, C58, C64, C67, C71, C73, C76, C80, C81, C82, C83, C87, C88: 100n; C_0603_HandSoldering
C10, C26, C30, C46, C47, C48, C49, C52, C65, C66, C68: 10n; C_0603_HandSoldering
C21, C72: 1n; C_0603_HandSoldering
C25, C27, C28, C69: 1u; C_0603_HandSoldering
C44: 10u, 10v; C_0805
C45, C84, C85: 10u, 6.3v; C_0805
C54: 4u7; C_0805
C59, C63, C77, C78: 47n; C_0603_HandSoldering
CN7: CONN_02X10; Socket_Strip_Straight_2x10_Pitch2.54mm
CN8: CONN_02X08; Socket_Strip_Straight_2x08_Pitch2.54mm
CN9: CONN_02X15; Socket_Strip_Straight_2x15_Pitch2.54mm
CN10: CONN_02X17; Socket_Strip_Straight_2x17_Pitch2.54mm
CON1: SD_Card; SD_Card_Receptacle
D1: SP0503BAHT; SOT-143R_Reverse_Handsoldering
D2, D6: 3.3V; D_SOD-523
D3, D4, D5, D19, D20, D21, D22, D23: SP0504BAHT; TSOT-23-5
D7, D14, D15, D16: Led_Small; LED_0603_HandSoldering
D8: PWM1; LED_0603_HandSoldering
D9: PWM2; LED_0603_HandSoldering
D10: PWM3; LED_0603_HandSoldering
D11: ~PWM1; LED_0603_HandSoldering
D12: ~PWM2; LED_0603_HandSoldering
D13: ~PWM3; LED_0603_HandSoldering
D17: TX; LED_0603_HandSoldering
D18: RX; LED_0603_HandSoldering
D24, D26: D_Schottky_x2_KCom_AAK; TSOT-23
D25: 1.5KExxA; D_SMB-SMC_Universal_Handsoldering
F1: Polyfuse; Fuse_1812_4532Metric_Pad1.24x3.50mm_HandSolder
FB1, FB6, FB7, FB8, FB9, FB10, FB11, FB12, FB13, FB14: FILTER; inductor_smd_0805
FI2, FI4, FI5: NFE61P; EMI_Filter_murata
FL1: Wurth_744273501; WE_SL5_HR_CommonMode_filter
I1, I2, I7, I8, I9: DS90LV027A; SOIC-8_3.9x4.9mm_Pitch1.27mm
I3, I4, I5, I6: DS90LV028A; SOIC-8_3.9x4.9mm_Pitch1.27mm
J1: USB_OTG; USB_Mini-B
J2: QSPI_CLK; Test_Point
J3: QSPI_NCS; Test_Point
J4: QSPI_IO0; Test_Point
J5: QSPI_IO1; Test_Point
J6: QSPI_IO2; Test_Point
J7: QSPI_IO3; Test_Point
J8: 12V; Test_Point
J9, J10, J11, J36, J37: GND; Test_Point
J12: 5V; Test_Point
J13: Regen; Test_Point
J14: Throttle; Test_Point
J15: PWM1; Test_Point
J16: PWM2; Test_Point
J17: PWM3; Test_Point
J18: ~PWM1; Test_Point
J19: ~PWM2; Test_Point
J20: ~PWM3; Test_Point
J21: OCV; Test_Point
J22: ~F_C; Test_Point
J23: ~F_B; Test_Point
J24: ~F_A; Test_Point
J25: Overtemp; Test_Point
J26: PWM_EN; Test_Point
J27: Conn_01x04_Female; TerminalBlock_Pheonix_PT-3.5mm_4pol
J28, J43, J44, J45, J46, J47, J48, J49, J50, J51, J52, J53, J54, J55: GS3
J29: Conn_01x04; PhoenixContact_MSTB-GF_04x5.08mm_Angled_ThreadedFlange_Moun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
J30: SPI2_SCK; Test_Point
J31: SPI2_NSS; Test_Point
J32: SPI2_MOSI; Test_Point
J33: SPI2_MISO; Test_Point
J34: PS-DIS; Test_Point
J35: 3V3; Test_Point
J38: AGND; Test_Point
J39: SP1_MISO; Test_Point
J40: SP1_SCK; Test_Point
J41: SP1_NSS; Test_Point
J42: SP1_MOSI; Test_Point
L1: BLM18PG121SN1D; inductor_smd_0603
L2, L3, L4, L5, L6, L7, L10, L11, L12, L13, L16, L17: 1uH; inductor_smd_0603
L9, L14, L15, L18: 10uH; Neosid_Inductor_SM-NE45_SMD1812
MK1, MK2, MK3, MK4: Mounting_Hole_PAD; MountingHole_4.3mm_M4_Pad_Via
MK5, MK6, MK7, MK8, MK9: Mounting_Hole; MountingHole_3.2mm_M3
OPT1, OPT2, OPT7, OPT8, OPT9: AFBR-1634Z; HFBR-xx2xZ
OPT3, OPT4, OPT5, OPT6, OPT10, OPT11: AFBR-26x; HFBR-xx2xZ
P1, P9, P10, P11: GATE_IO_A; IDC-Header_2x08_Pitch2.54mm_Straight
P7: CONN_01X02; TerminalBlock_Pheonix_PT-3.5mm_2pol
R1, R2, R5, R6, R7, R10, R33, R34, R35: 4k7; R_0603_HandSoldering
R3, R4: ?; R_0603_HandSoldering
R8, R14, R18, R19, R20, R21, R22, R23, R55: 240; R_0603_HandSoldering
R9, R11, R12, R15, R16, R17, R29, R30, R32, R36, R37, R57, R58: DNP; R_0603_HandSoldering
R13: 1k; R_0603_HandSoldering
R24, R25, R26, R27, R28, R31: 47k; R_0603_HandSoldering
R38, R59: 0R; R_0603_HandSoldering
R39, R40, R45, R46, R60, R61, R62, R63, R64, R65: 680; R_0603_HandSoldering
R41, R42, R43, R44, R67: 10k; R_0603_HandSoldering
R51, R52, R53, R66: 0; R_0603_HandSoldering
U1: LM1117-5.0; TO-263-3_TabPin2
U2: LM1117-3.3; TO-263-3_TabPin2
U3: MCP101-315D; SOT-23_Handsoldering
U4: LTV-356T; DIP-6_W7.62mm_SMD
U5: ISO7221; SOIC-8_3.9x4.9mm_Pitch1.27mm
U6, U12, U13, U14, U15, U16, U17, U18, U19, U21: 74LVC1G02; SOT-353_SC-70-5_Handsoldering
U7: OPA2340; SOIC-8_3.9x4.9mm_Pitch1.27mm
U8: LM339; SOIC-14_3.9x8.7mm_Pitch1.27mm
U9: CD4043B; SOIC-16_3.9x9.9mm_Pitch1.27mm
U10: 74HC266; SOIC-14_3.9x8.7mm_Pitch1.27mm
U11: FT232RL; SSOP-28_5.3x10.2mm_Pitch0.65mm

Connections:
+3V3: C1.2, C2.2, C3.2, C4.2, C5.2, C6.2, C8.2, C9.2, C26.1, C31.2, C32.2, C33.2, C34.2, C35.2, C45.1, C46.1, C47.1, C48.1, C49.1, C52.1, C53.2, C56.2, C57.2, C58.2, C65.1, C66.1, C67.2, C68.1, C73.2, C74.2, C76.2, C79.2, C81.2, C82.2, C83.1, C87.2, C88.2, CON1.4 (VDD), FB1.1, I1.1 (VCC), I2.1 (VCC), I3.8 (VCC), I4.8 (VCC), I5.8 (VCC), I6.8 (VCC), I7.1 (VCC), I8.1 (VCC), I9.1 (VCC), J28.3 (B), J35.1, J43.3 (B), J44.1 (A), J45.1 (A), J46.1 (A), J47.1 (A), J48.3 (B), J49.3 (B), J50.3 (B), J51.1 (A), J52.3 (B), J53.3 (B), J54.3 (B), J55.3 (B), L2.2, L3.2, L4.2, L5.2, L6.2, L7.2, L10.2, L11.2, L12.2, L13.2, L17.1, L18.2, R10.2, R16.1, R24.1, R25.1, R26.1, R27.1, R28.1, R31.1, R43.1, R44.1, U2.2 (VO), U3.2 (VDD), U5.1 (VDD1), U6.5 (VCC), U8.3 (V+), U9.5 (Enable), U9.16 (VCC), U10.14 (VDD), U12.5 (VCC), U13.5 (VCC), U14.5 (VCC), U15.5 (VCC), U16.5 (VCC), U17.5 (VCC), U18.5 (VCC), U19.5 (VCC), U21.5 (VCC)
+5V: C44.1, J12.1, L9.1, R17.1, U1.2 (VO)
+12V: C7.1, C21.1, D25.1 (A1), F1.1, FI2.1 (VI), J8.1, P9.1, P10.1, P11.1, R15.1
+12VA: C29.1, C30.1, C69.1, FI2.3 (VO), L14.1, L15.1, L16.2
/12V_thr: C70.1, C71.2, C72.1, J27.4, L16.1, R9.2, R29.2, U7.8 (V+)
/ADC1_INP10_PC0: C61.1, CN9.3, R34.2, U8.7 (+)
/ADC1_INP13_PC3: CN9.5, D2.1 (K), J13.1, R59.1, U7.1
/ADC1_INP15_PA3: C60.1, CN9.1, R33.2, U8.5 (+)
/ADC1_INP18_PA4: C62.1, CN7.17, R35.2, U8.11 (+)
/ADC2_INP5_PB1: CN10.7, D6.1 (K), J14.1, R38.1, U7.7
/Fault_A+: D5.1 (K), I4.1 (R-), P9.7, R18.2
/Fault_A-: D5.3 (K), I4.2 (R+), P9.8, R18.1
/Fault_B+: D19.1 (K), I5.1 (R-), P10.7, R20.2
/Fault_B-: D19.3 (K), I5.2 (R+), P10.8, R20.1
/Fault_C+: D20.1 (K), I6.1 (R-), P11.7, R22.2
/Fault_C-: D20.3 (K), I6.2 (R+), P11.8, R22.1
/Fault_Gate_A: FB12.2, J24.1, U9.4 (S1)
/Fault_Gate_B: FB13.2, J23.1, U9.6 (S2)
/Fault_Gate_C: FB14.2, J22.1, U9.12 (S3)
/Fault_OCV: J21.1, R41.1, U9.14 (S4), U10.1, U10.11
/GPIO_EXTI3_PG3: CN8.16, R10.1, U4.6
/GPIO_EXTI13_PF13: CN10.2, R41.2
/GPIO_EXTI14_PF14: CN10.8, D24.3 (K), D26.3 (K), R42.2
/GPIO_OUTPUT_PF15: CN10.12, U9.3 (R1), U9.7 (R1), U9.11 (R2), U9.15 (R3)
/GPIO_Output_PG0: CN9.29, R44.2, U10.8
/OverTemp_trip: J25.1, R43.2, U8.1, U8.2, U8.13, U10.5
/PWMA_HS+: D22.4 (K), I7.7 (DO+), P9.3
/PWMA_HS-: D22.3 (K), I7.8 (D0-), P9.4
/PWMA_LS+: D22.5 (K), I7.6 (DO+), P9.5
/PWMA_LS-: D22.1 (K), I7.5 (DO-), P9.6
/PWMB_HS+: D23.4 (K), I8.7 (DO+), P10.3
/PWMB_HS-: D23.3 (K), I8.8 (D0-), P10.4
/PWMB_LS+: D23.5 (K), I8.6 (DO+), P10.5
/PWMB_LS-: D23.1 (K), I8.5 (DO-), P10.6
/PWMC_HS+: D21.4 (K), I9.7 (DO+), P11.3
/PWMC_HS-: D21.3 (K), I9.8 (D0-), P11.4
/PWMC_LS+: D21.5 (K), I9.6 (DO+), P11.5
/PWMC_LS-: D21.1 (K), I9.5 (DO-), P11.6
/PWM_EN: CN9.16, J26.1, P9.13, P10.13, P11.13, U10.3, U10.4, U10.10
/QUADSPI_BK1_IO0_PD11: CN10.23, J4.1, U12.4
/QUADSPI_BK1_IO1_PD12: CN10.21, J5.1, U13.4
/QUADSPI_BK1_IO2_PE2: CN10.25, J6.1, U14.4
/QUADSPI_BK1_IO3_PD13: CN10.19, J7.1, U15.4
/QUADSPI_BK1_NCS_PB10: CN10.32, U6.1
/QUADSPI_CLK_PB2: CN10.15, U21.1
/RTD_A+: D5.4 (K), I4.3 (R+), P9.9, R19.2
/RTD_A-: D5.5 (K), I4.4 (R-), P9.10, R19.1
/RTD_B+: D19.4 (K), I5.3 (R+), P10.9, R21.2
/RTD_B-: D19.5 (K), I5.4 (R-), P10.10, R21.1
/RTD_C+: D20.4 (K), I6.3 (R+), P11.9, R23.2
/RTD_C-: D20.5 (K), I6.4 (R-), P11.10, R23.1
/RTD_trip_ref: C64.1, R67.2, U8.4 (-), U8.6 (-), U8.10 (-)
/Regen_In: FI5.1 (VI), J27.3
/SDMMC1_CK_PC12: CN8.10, FB9.1, R27.2
/SDMMC1_CMD_PD2: CN8.12, FB8.1, R26.2
/SDMMC1_D0_PC8: CN8.2, FB10.1, R28.2
/SDMMC1_D1_PC9: CN8.4, FB11.1, R31.2
/SDMMC1_D2_PC10: CN8.6, FB6.1, R24.2
/SDMMC1_D3_PC11: CN8.8, FB7.1, R25.2
/SP1_MISO+: D4.3 (K), I3.2 (R+), P1.3, R8.1
/SP1_MISO-: D4.4 (K), I3.1 (R-), P1.4, R8.2
/SP1_MISO_PA6: CN7.12, J39.1, P1.14, R66.1
/SP1_MOSI+: D4.1 (K), I2.6 (DO+), P1.5
/SP1_MOSI-: D4.5 (K), I2.5 (DO-), P1.6
/SP1_MOSI_PB5: CN7.13, I2.3 (DI2), J42.1, P1.12
/SP2_MISO_PC2: CN10.9, J33.1, U19.4
/SP2_MOSI_PB15: CN7.3, U18.1
/SPI1_NSS+: D3.3 (K), I1.6 (DO+), P1.9
/SPI1_NSS-: D3.1 (K), I1.5 (DO-), P1.10
/SPI1_NSS_PA15: CN7.9, I1.3 (DI2), J41.1, P1.13
/SPI1_SCK+: D3.4 (K), I1.7 (DO+), P1.7
/SPI1_SCK-: D3.5 (K), I1.8 (D0-), P1.8
/SPI1_SCK_PA5: CN7.10, I1.2 (DI1), J40.1, P1.11
/SPI2_NSS_PB4: CN7.19, U17.1
/SPI2_SCK_PD3: CN9.10, U16.1
/TMR1_CH1N_PE8: CN10.18, I7.3 (DI2), J18.1, R63.1
/TMR1_CH1_PE9: CN10.4, I7.2 (DI1), J15.1, R60.1
/TMR1_CH2N_PE10: CN10.24, I8.3 (DI2), J19.1, R64.1
/TMR1_CH2_PE11: CN10.6, I8.2 (DI1), J16.1, R61.1
/TMR1_CH3N_PE12: CN10.26, I9.3 (DI2), J20.1, R65.1
/TMR1_CH3_PE13: CN10.10, I9.2 (DI1), J17.1, R62.1
/USART6_RX_PG9: CN10.16, U5.3 (VIB)
/USART6_TX_PG14: CN10.14, U5.2 (VOA)
/~PS-Dis: J34.1, P9.11, P10.11, P11.11, U3.1 (RST)
AGND: C63.2, C69.2, C70.2, C71.1, C72.2, C78.2, CN10.3, D2.2 (A), D6.2 (A), FI4.2 (GND), FI5.2 (GND), J27.1, J38.1, R11.1, R30.1, R37.1, R58.1, U7.4 (V-)
DGND: C1.1, C2.1, C3.1, C4.1, C5.1, C6.1, C7.2, C8.1, C9.1, C11.1, C12.1, C13.1, C14.1, C15.1, C16.1, C17.1, C18.1, C19.1, C20.1, C21.2, C22.1, C23.1, C25.2, C26.2, C27.2, C28.2, C29.2, C30.2, C31.1, C32.1, C33.1, C34.1, C35.1, C36.1, C37.1, C38.1, C39.1, C40.1, C41.1, C42.1, C43.1, C44.2, C45.2, C46.2, C47.2, C48.2, C49.2, C52.2, C53.1, C56.1, C57.1, C58.1, C60.2, C61.2, C62.2, C64.2, C65.2, C66.2, C67.1, C68.2, C73.1, C74.1, C75.1, C76.1, C79.1, C80.1, C81.1, C82.1, C83.2, C84.2, C85.2, C87.1, C88.1, CN7.8, CN8.11, CN8.13, CN9.9, CN9.23, CN10.5, CN10.17, CN10.22, CN10.27, CON1.3 (VSS), CON1.6 (VSS), CON1.12 (SHELL1), CON1.13 (SHELL2), D3.2 (A), D4.2 (A), D5.2 (A), D7.1 (K), D8.1 (K), D9.1 (K), D10.1 (K), D11.1 (K), D12.1 (K), D13.1 (K), D14.1 (K), D15.1 (K), D16.1 (K), D19.2 (A), D20.2 (A), D21.2 (A), D22.2 (A), D23.2 (A), D25.2 (A2), FI2.2 (GND), FL1.4, I1.4 (GND), I2.2 (DI1), I2.4 (GND), I3.5 (GND), I4.5 (GND), I5.5 (GND), I6.5 (GND), I7.4 (GND), I8.4 (GND), I9.4 (GND), J9.1, J10.1, J11.1, J28.1 (A), J36.1, J37.1, J43.1 (A), J44.3 (B), J45.3 (B), J46.3 (B), J47.3 (B), J48.1 (A), J49.1 (A), J50.1 (A), J51.3 (B), J52.1 (A), J53.1 (A), J54.1 (A), J55.1 (A), MK1.1, MK2.1, MK3.1, MK4.1, OPT1.3 (VEE), OPT1.5 (Gnd), OPT1.8 (Gnd), OPT2.3 (VEE), OPT2.5 (Gnd), OPT2.8 (Gnd), OPT3.2 (Vee), OPT3.5 (Gnd), OPT3.8 (Gnd), OPT4.2 (Vee), OPT4.5 (Gnd), OPT4.8 (Gnd), OPT5.2 (Vee), OPT5.5 (Gnd), OPT5.8 (Gnd), OPT6.2 (Vee), OPT6.5 (Gnd), OPT6.8 (Gnd), OPT7.3 (VEE), OPT7.5 (Gnd), OPT7.8 (Gnd), OPT8.3 (VEE), OPT8.5 (Gnd), OPT8.8 (Gnd), OPT9.3 (VEE), OPT9.5 (Gnd), OPT9.8 (Gnd), OPT10.2 (Vee), OPT10.5 (Gnd), OPT10.8 (Gnd), OPT11.2 (Vee), OPT11.5 (Gnd), OPT11.8 (Gnd), P1.2, P1.16, P9.2, P9.12, P9.14, P9.16, P10.2, P10.12, P10.14, P10.16, P11.2, P11.12, P11.14, P11.16, R1.1, R2.1, R4.1, R5.1, R6.1, R7.1, R42.1, R51.2, R52.2, R53.2, U1.1 (GND), U2.1 (GND), U3.3 (VSS), U4.4, U5.4 (GND1), U6.3 (GND), U8.12 (V-), U9.8 (GND), U10.7 (VSS), U12.3 (GND), U13.3 (GND), U14.3 (GND), U15.3 (GND), U16.3 (GND), U17.3 (GND), U18.3 (GND), U19.3 (GND), U21.3 (GND)
unnamed: C10.1, D1.2 (K), J1.1 (VBUS), L1.2
unnamed: C10.2, C24.2, C51.2, C54.2, C55.2, D1.1 (A), J1.5 (GND), J1.6 (Shield), U5.5 (GND2), U11.7 (GND), U11.18 (GND), U11.21 (GND), U11.25 (AGND), U11.26 (TEST)
unnamed: C11.2, C17.2, L2.1, OPT3.3 (Vcc)
unnamed: C12.2, C18.2, L3.1, OPT4.3 (Vcc)
unnamed: C13.2, C19.2, L4.1, OPT5.3 (Vcc)
unnamed: C14.2, C20.2, L5.1, OPT6.3 (Vcc)
unnamed: C15.2, C22.2, L6.1, OPT1.1 (Vcc)
unnamed: C16.2, C23.2, L7.1, OPT2.1 (Vcc)
unnamed: C24.1, U11.17 (3V3OUT)
unnamed: C25.1, R3.1, R4.2, R67.1
unnamed: C27.1, L14.2, U1.3 (VI)
unnamed: C28.1, L15.2, U2.3 (VI)
unnamed: C36.2, C40.2, L10.1, OPT10.3 (Vcc)
unnamed: C37.2, C41.2, L11.1, OPT7.1 (Vcc)
unnamed: C38.2, C42.2, L12.1, OPT8.1 (Vcc)
unnamed: C39.2, C43.2, L13.1, OPT9.1 (Vcc)
unnamed: C51.1, C54.1, C55.1, L1.1, R14.2, R55.2, U5.8 (VDD2), U11.4 (VCCIO), U11.20 (VCC)
unnamed: C59.1, R37.2, R38.2, U7.6 (-)
unnamed: C59.2, R32.1, R36.2
unnamed: C63.1, R36.1, U7.5 (+)
unnamed: C75.2, C80.2, L17.2, OPT11.3 (Vcc)
unnamed: C77.1, R58.2, R59.2, U7.2 (-)
unnamed: C77.2, R12.1, R57.2
unnamed: C78.1, R57.1, U7.3 (+)
unnamed: C84.1, L9.2, P1.1
unnamed: C85.1, L18.1, P1.15
unnamed: CN8.5, R15.2
unnamed: CN8.7, R16.2
unnamed: CN8.9, R17.2
unnamed: CON1.1 (CD/DAT3), FB7.2
unnamed: CON1.2 (CMD), FB8.2
unnamed: CON1.5 (CLK), FB9.2
unnamed: CON1.7 (DAT0), FB10.2
unnamed: CON1.8 (DAT1), FB11.2
unnamed: CON1.9 (DAT2), FB6.2
unnamed: D1.3 (K), J1.2 (D-), U11.16 (USBD-)
unnamed: D1.4 (K), J1.3 (D+), U11.15 (USBD+)
unnamed: D7.2 (A), R39.1
unnamed: D8.2 (A), R60.2
unnamed: D9.2 (A), R61.2
unnamed: D10.2 (A), R62.2
unnamed: D11.2 (A), R63.2
unnamed: D12.2 (A), R64.2
unnamed: D13.2 (A), R65.2
unnamed: D14.2 (A), R40.1
unnamed: D15.2 (A), R45.1
unnamed: D16.2 (A), R46.1
unnamed: D17.1 (K), U11.23 (CBUS0)
unnamed: D17.2 (A), R55.1
unnamed: D18.1 (K), U11.22 (CBUS1)
unnamed: D18.2 (A), R14.1
unnamed: D24.1 (A), R39.2, U9.2 (Q0)
unnamed: D24.2 (A), R46.2, U9.1 (Q3)
unnamed: D26.1 (A), R45.2, U9.10 (Q2)
unnamed: D26.2 (A), R40.2, U9.9 (Q1)
unnamed: F1.2, FL1.2
unnamed: FB1.2, R3.2
unnamed: FB12.1, I4.7 (Ro1)
unnamed: FB13.1, I5.7 (Ro1)
unnamed: FB14.1, I6.7 (Ro1)
unnamed: FI4.1 (VI), J27.2
unnamed: FI4.3 (VO), R29.1, R30.2, R32.2
unnamed: FI5.3 (VO), R9.1, R11.2, R12.2
unnamed: FL1.1, J29.3, J29.4
unnamed: FL1.3, J29.1, J29.2
unnamed: I3.7 (Ro1), R66.2
unnamed: I4.6 (Ro2), R33.1
unnamed: I5.6 (Ro2), R34.1
unnamed: I6.6 (Ro2), R35.1
unnamed: J2.1, OPT1.4 (Data_in), R1.2, U21.4
unnamed: J3.1, OPT2.4 (Data_in), R2.2, U6.4
unnamed: J28.2 (C), U21.2
unnamed: J30.1, OPT7.4 (Data_in), R5.2, U16.4
unnamed: J31.1, OPT8.4 (Data_in), R6.2, U17.4
unnamed: J32.1, OPT9.4 (Data_in), R7.2, U18.4
unnamed: J43.2 (C), U6.2
unnamed: J44.2 (C), U12.2
unnamed: J45.2 (C), U13.2
unnamed: J46.2 (C), U14.2
unnamed: J47.2 (C), U15.2
unnamed: J48.2 (C), U16.2
unnamed: J49.2 (C), U17.2
unnamed: J50.2 (C), U18.2
unnamed: J51.2 (C), U19.2
unnamed: J52.2 (C), U10.12
unnamed: J53.2 (C), U10.6
unnamed: J54.2 (C), U10.9
unnamed: J55.2 (C), U10.2
unnamed: OPT3.1 (Data_Out), U12.1
unnamed: OPT4.1 (Data_Out), U13.1
unnamed: OPT5.1 (Data_Out), U14.1
unnamed: OPT6.1 (Data_Out), U15.1
unnamed: OPT10.1 (Data_Out), U19.1
unnamed: OPT11.1 (Data_Out), U10.13
unnamed: P7.1, R13.1
unnamed: P7.2, U4.3
unnamed: P9.15, R51.1
unnamed: P10.15, R52.1
unnamed: P11.15, R53.1
unnamed: R13.2, U4.1
unnamed: U5.7 (VIA), U11.1 (TXD)
unnamed: U5.6 (VOB), U11.5 (RXD)

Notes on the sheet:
Fault in (overcurrent)
UART
Throttle
Chip Select
Clock
Data in
Data out
PCB stackup: - LVDS signals - GROUND - SUPPLY - TTL
Current sensing - quad SPI
SPI2 (Spare)
Filter / 22R resistor
Encoder, BiSS (SPI1)
ESTOP
Fault logic
PWM
Gate driver faults
Supply
Nucleo-H743ZI connections
Driven by AM26C31
Regen
SHB11-PBPC-D08-ST-BK
Fault signals intentionally inverted for failsafe when unplugging

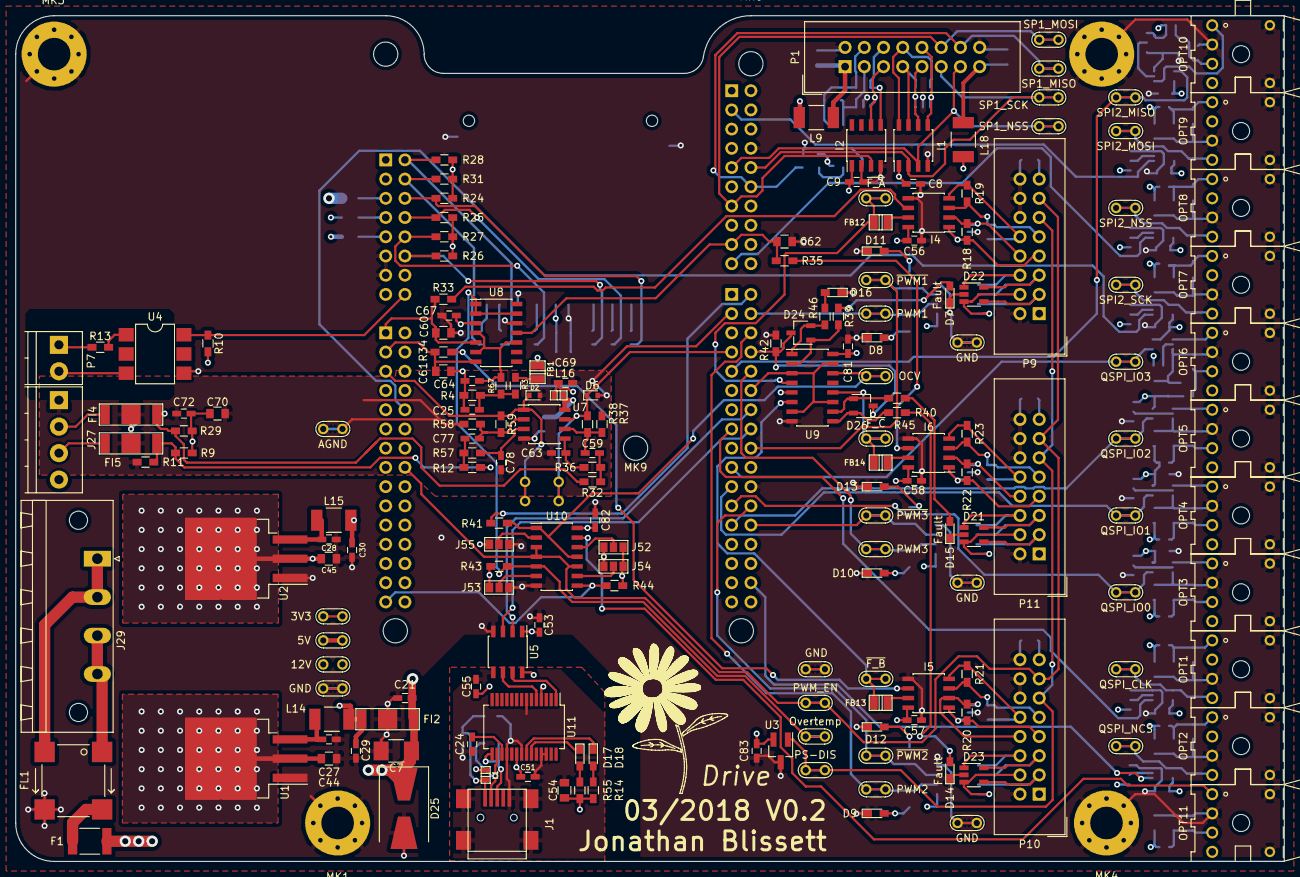
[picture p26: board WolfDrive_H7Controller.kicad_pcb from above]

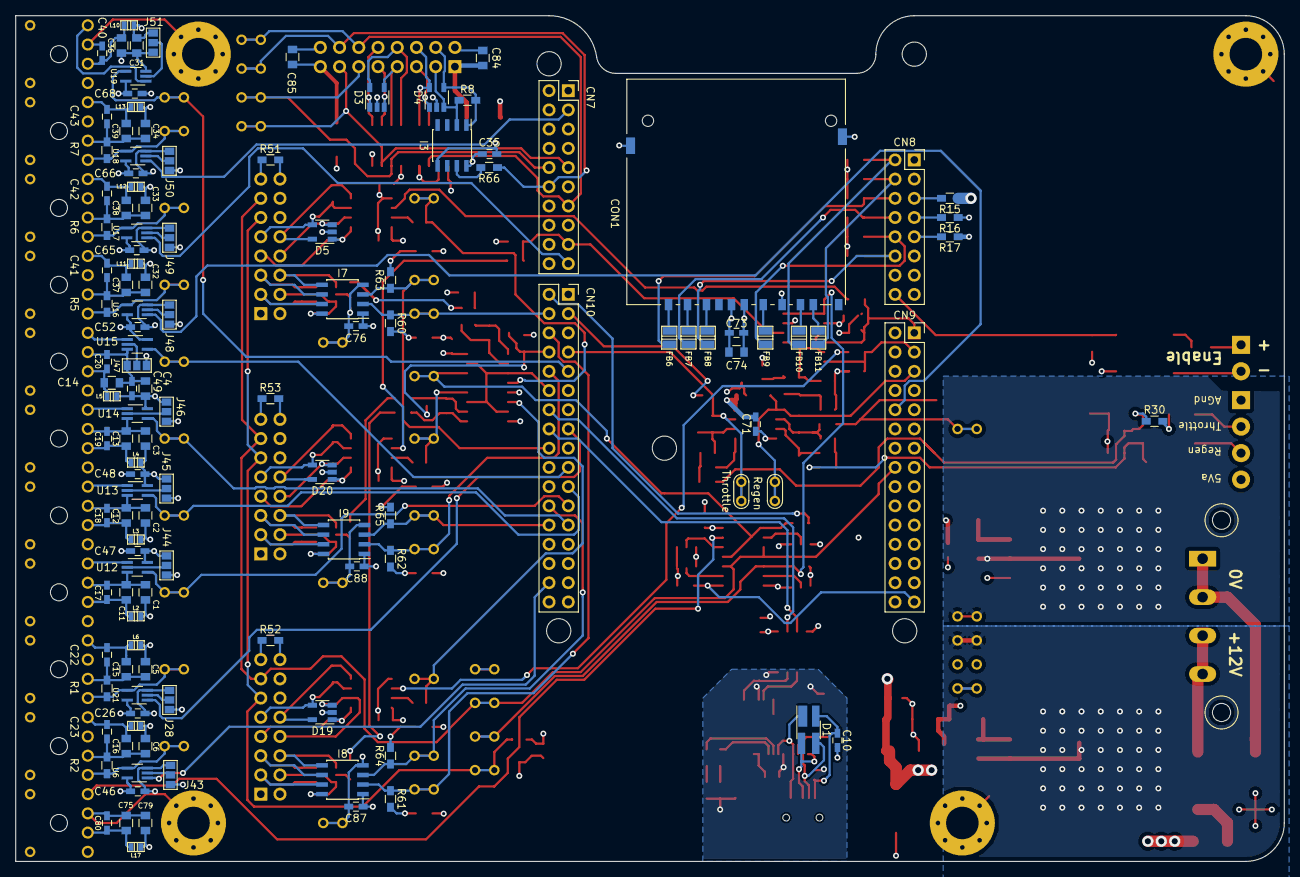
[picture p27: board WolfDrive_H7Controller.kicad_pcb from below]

Board: 4 copper layers, 167.6 x 111.8 mm, 319 parts (126 on the bottom side), 188 nets.

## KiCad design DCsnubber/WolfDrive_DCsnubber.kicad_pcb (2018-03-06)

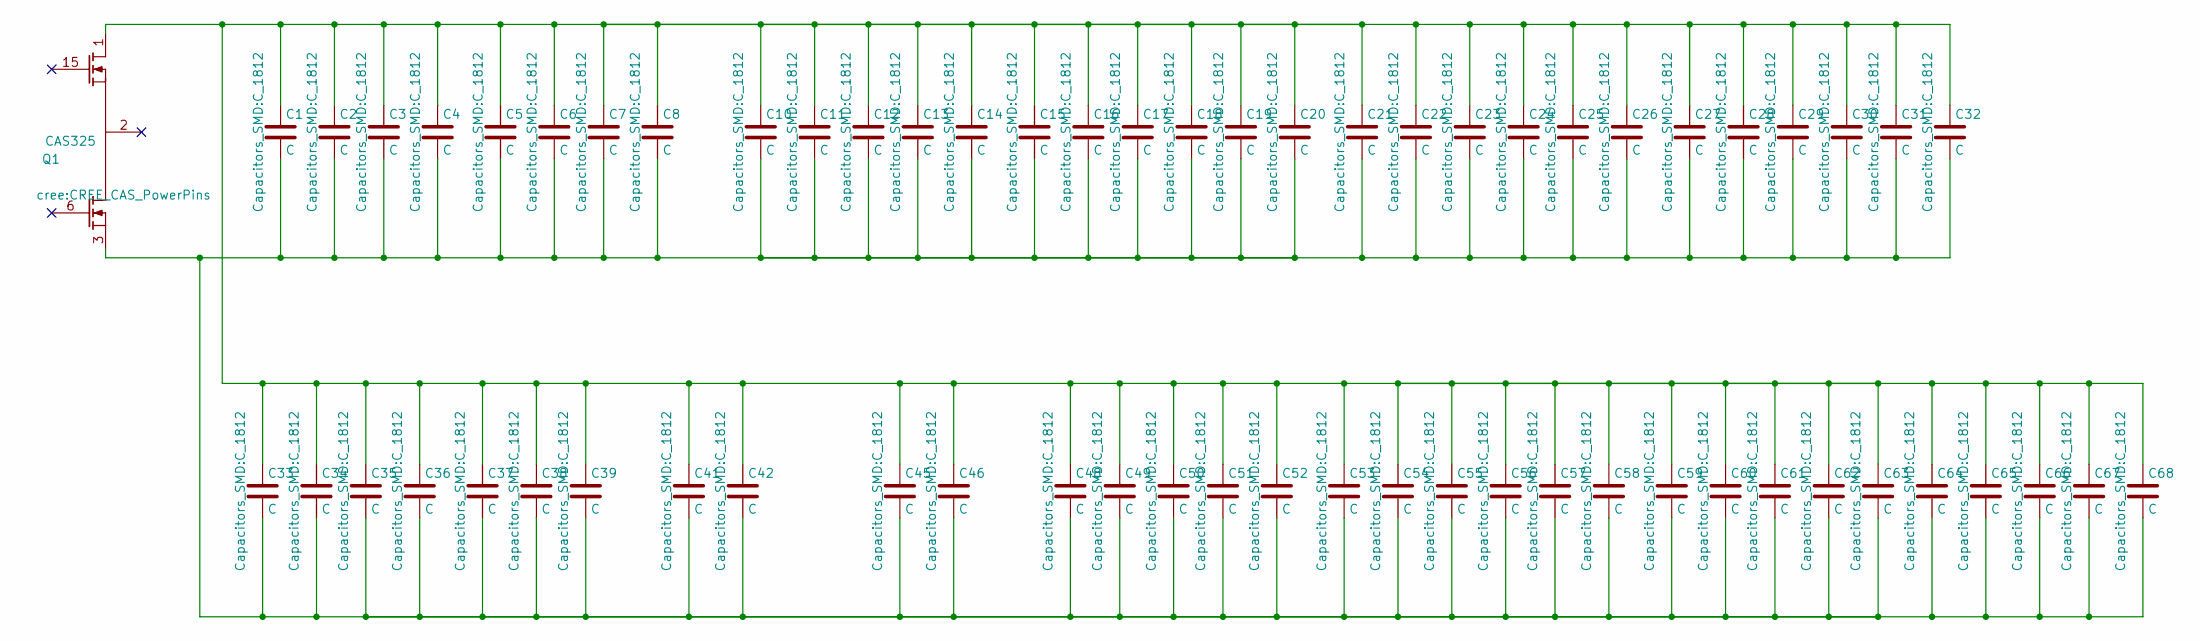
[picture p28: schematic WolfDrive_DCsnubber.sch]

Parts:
C1, C2, C3, C4, C5, C6, C7, C8, C10, C11, C12, C13, C14, C15, C16, C17, C18, C19, C20, C21, C22, C23, C24, C25, C26, C27, C28, C29, C30, C31, C32, C33, C34, C35, C36, C37, C38, C39, C41, C42, C45, C46, C48, C49, C50, C51, C52, C53, C54, C55, C56, C57, C58, C59, C60, C61, C62, C63, C64, C65, C66, C67, C68: C; C_1812
Q1: CAS325; CREE_CAS_PowerPins

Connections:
unnamed: C1.1, C2.1, C3.1, C4.1, C5.1, C6.1, C7.1, C8.1, C10.1, C11.1, C12.1, C13.1, C14.1, C15.1, C16.1, C17.1, C18.1, C19.1, C20.1, C21.1, C22.1, C23.1, C24.1, C25.1, C26.1, C27.1, C28.1, C29.1, C30.1, C31.1, C32.1, C33.1, C34.1, C35.1, C36.1, C37.1, C38.1, C39.1, C41.1, C42.1, C45.1, C46.1, C48.1, C49.1, C50.1, C51.1, C52.1, C53.1, C54.1, C55.1, C56.1, C57.1, C58.1, C59.1, C60.1, C61.1, C62.1, C63.1, C64.1, C65.1, C66.1, C67.1, C68.1, Q1.1 (D)
unnamed: C1.2, C2.2, C3.2, C4.2, C5.2, C6.2, C7.2, C8.2, C10.2, C11.2, C12.2, C13.2, C14.2, C15.2, C16.2, C17.2, C18.2, C19.2, C20.2, C21.2, C22.2, C23.2, C24.2, C25.2, C26.2, C27.2, C28.2, C29.2, C30.2, C31.2, C32.2, C33.2, C34.2, C35.2, C36.2, C37.2, C38.2, C39.2, C41.2, C42.2, C45.2, C46.2, C48.2, C49.2, C50.2, C51.2, C52.2, C53.2, C54.2, C55.2, C56.2, C57.2, C58.2, C59.2, C60.2, C61.2, C62.2, C63.2, C64.2, C65.2, C66.2, C67.2, C68.2, Q1.3 (S)

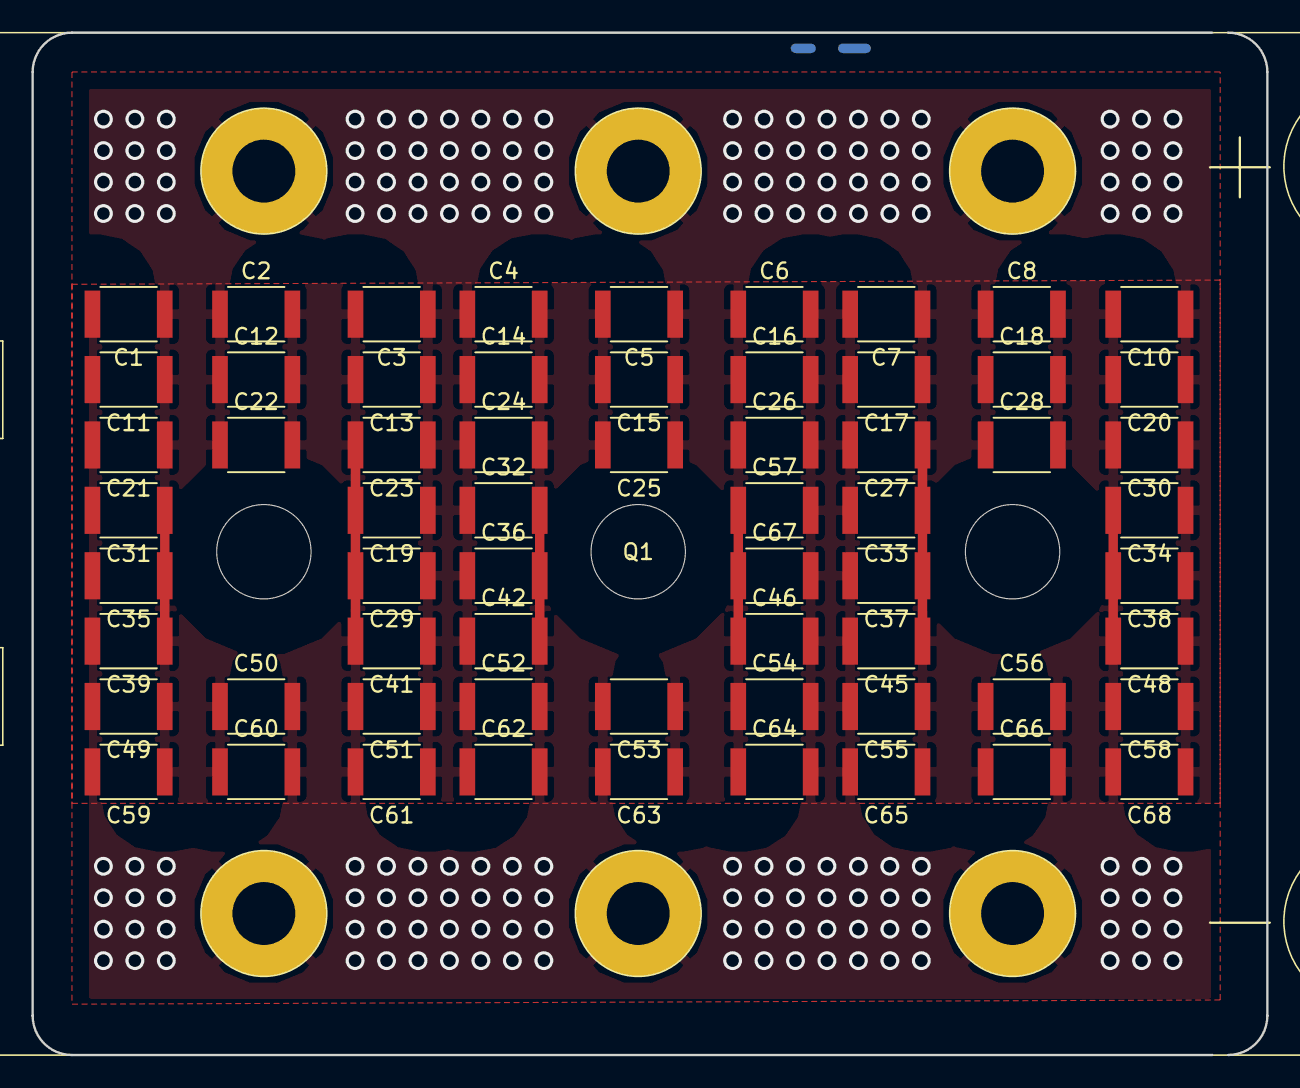
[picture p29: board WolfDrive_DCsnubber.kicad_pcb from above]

Board: 2 copper layers, 78.5 x 65.0 mm, 64 parts (0 on the bottom side), 2 nets.

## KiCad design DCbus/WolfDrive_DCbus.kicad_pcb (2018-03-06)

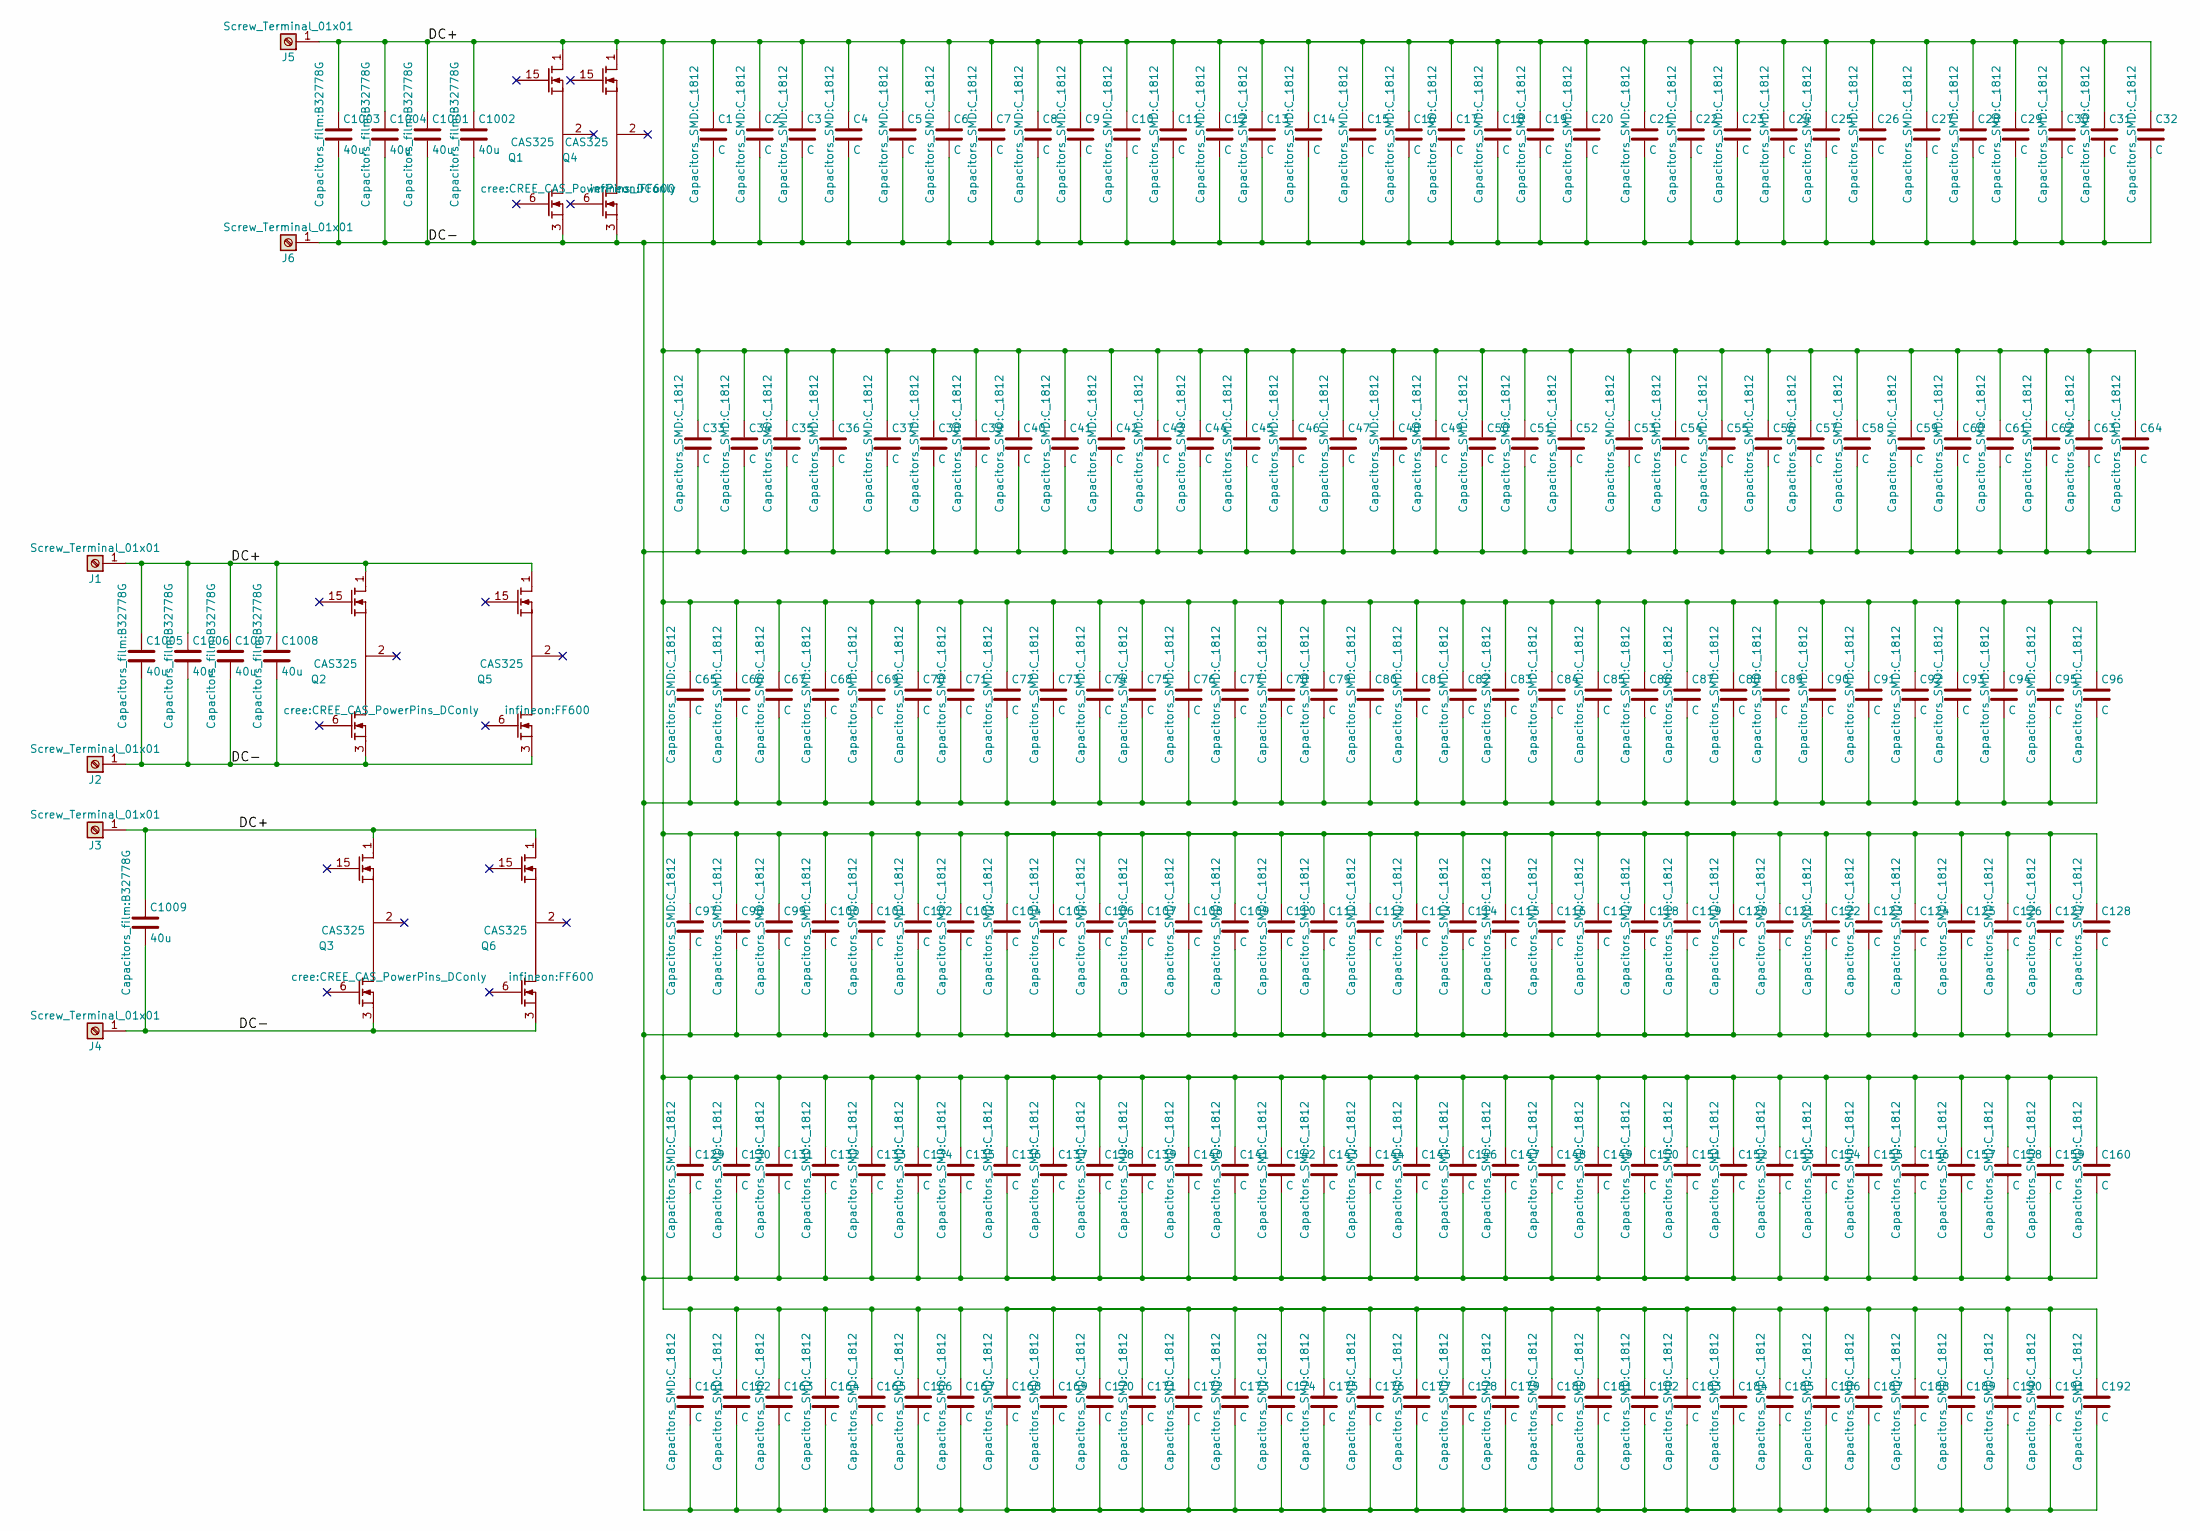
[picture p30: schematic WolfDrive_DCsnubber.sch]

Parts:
C1, C2, C3, C4, C5, C6, C7, C8, C9, C10, C11, C12, C13, C14, C15, C16, C17, C18, C19, C20, C21, C22, C23, C24, C25, C26, C27, C28, C29, C30, C31, C32, C33, C34, C35, C36, C37, C38, C39, C40, C41, C42, C43, C44, C45, C46, C47, C48, C49, C50, C51, C52, C53, C54, C55, C56, C57, C58, C59, C60, C61, C62, C63, C64, C65, C66, C67, C68, C69, C70, C71, C72, C73, C74, C75, C76, C77, C78, C79, C80, C81, C82, C83, C84, C85, C86, C87, C88, C89, C90, C91, C92, C93, C94, C95, C96, C97, C98, C99, C100, C101, C102, C103, C104, C105, C106, C107, C108, C109, C110, C111, C112, C113, C114, C115, C116, C117, C118, C119, C120, C121, C122, C123, C124, C125, C126, C127, C128, C129, C130, C131, C132, C133, C134, C135, C136, C137, C138, C139, C140, C141, C142, C143, C144, C145, C146, C147, C148, C149, C150, C151, C152, C153, C154, C155, C156, C157, C158, C159, C160, C161, C162, C163, C164, C165, C166, C167, C168, C169, C170, C171, C172, C173, C174, C175, C176, C177, C178, C179, C180, C181, C182, C183, C184, C185, C186, C187, C188, C189, C190, C191, C192: C; C_1812
C1001, C1002, C1003, C1004, C1005, C1006, C1007, C1008, C1009: 40u; B32778G
J1, J2, J3, J4, J5, J6: Screw_Terminal_01x01; PowerOne_16x16mm_24pin
Q1, Q2, Q3: CAS325; CREE_CAS_PowerPins_DConly
Q4, Q5, Q6: CAS325; FF600

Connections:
/DC+: C1.1, C2.1, C3.1, C4.1, C5.1, C6.1, C7.1, C8.1, C9.1, C10.1, C11.1, C12.1, C13.1, C14.1, C15.1, C16.1, C17.1, C18.1, C19.1, C20.1, C21.1, C22.1, C23.1, C24.1, C25.1, C26.1, C27.1, C28.1, C29.1, C30.1, C31.1, C32.1, C33.1, C34.1, C35.1, C36.1, C37.1, C38.1, C39.1, C40.1, C41.1, C42.1, C43.1, C44.1, C45.1, C46.1, C47.1, C48.1, C49.1, C50.1, C51.1, C52.1, C53.1, C54.1, C55.1, C56.1, C57.1, C58.1, C59.1, C60.1, C61.1, C62.1, C63.1, C64.1, C65.1, C66.1, C67.1, C68.1, C69.1, C70.1, C71.1, C72.1, C73.1, C74.1, C75.1, C76.1, C77.1, C78.1, C79.1, C80.1, C81.1, C82.1, C83.1, C84.1, C85.1, C86.1, C87.1, C88.1, C89.1, C90.1, C91.1, C92.1, C93.1, C94.1, C95.1, C96.1, C97.1, C98.1, C99.1, C100.1, C101.1, C102.1, C103.1, C104.1, C105.1, C106.1, C107.1, C108.1, C109.1, C110.1, C111.1, C112.1, C113.1, C114.1, C115.1, C116.1, C117.1, C118.1, C119.1, C120.1, C121.1, C122.1, C123.1, C124.1, C125.1, C126.1, C127.1, C128.1, C129.1, C130.1, C131.1, C132.1, C133.1, C134.1, C135.1, C136.1, C137.1, C138.1, C139.1, C140.1, C141.1, C142.1, C143.1, C144.1, C145.1, C146.1, C147.1, C148.1, C149.1, C150.1, C151.1, C152.1, C153.1, C154.1, C155.1, C156.1, C157.1, C158.1, C159.1, C160.1, C161.1, C162.1, C163.1, C164.1, C165.1, C166.1, C167.1, C168.1, C169.1, C170.1, C171.1, C172.1, C173.1, C174.1, C175.1, C176.1, C177.1, C178.1, C179.1, C180.1, C181.1, C182.1, C183.1, C184.1, C185.1, C186.1, C187.1, C188.1, C189.1, C190.1, C191.1, C192.1, C1001.1, C1002.1, C1003.1, C1004.1, C1005.1, C1006.1, C1007.1, C1008.1, C1009.1, J1.1, J3.1, J5.1, Q1.1 (D), Q2.1 (D), Q3.1 (D), Q4.1 (D), Q5.1 (D), Q6.1 (D); also elsewhere on the board
/DC-: C1.2, C2.2, C3.2, C4.2, C5.2, C6.2, C7.2, C8.2, C9.2, C10.2, C11.2, C12.2, C13.2, C14.2, C15.2, C16.2, C17.2, C18.2, C19.2, C20.2, C21.2, C22.2, C23.2, C24.2, C25.2, C26.2, C27.2, C28.2, C29.2, C30.2, C31.2, C32.2, C33.2, C34.2, C35.2, C36.2, C37.2, C38.2, C39.2, C40.2, C41.2, C42.2, C43.2, C44.2, C45.2, C46.2, C47.2, C48.2, C49.2, C50.2, C51.2, C52.2, C53.2, C54.2, C55.2, C56.2, C57.2, C58.2, C59.2, C60.2, C61.2, C62.2, C63.2, C64.2, C65.2, C66.2, C67.2, C68.2, C69.2, C70.2, C71.2, C72.2, C73.2, C74.2, C75.2, C76.2, C77.2, C78.2, C79.2, C80.2, C81.2, C82.2, C83.2, C84.2, C85.2, C86.2, C87.2, C88.2, C89.2, C90.2, C91.2, C92.2, C93.2, C94.2, C95.2, C96.2, C97.2, C98.2, C99.2, C100.2, C101.2, C102.2, C103.2, C104.2, C105.2, C106.2, C107.2, C108.2, C109.2, C110.2, C111.2, C112.2, C113.2, C114.2, C115.2, C116.2, C117.2, C118.2, C119.2, C120.2, C121.2, C122.2, C123.2, C124.2, C125.2, C126.2, C127.2, C128.2, C129.2, C130.2, C131.2, C132.2, C133.2, C134.2, C135.2, C136.2, C137.2, C138.2, C139.2, C140.2, C141.2, C142.2, C143.2, C144.2, C145.2, C146.2, C147.2, C148.2, C149.2, C150.2, C151.2, C152.2, C153.2, C154.2, C155.2, C156.2, C157.2, C158.2, C159.2, C160.2, C161.2, C162.2, C163.2, C164.2, C165.2, C166.2, C167.2, C168.2, C169.2, C170.2, C171.2, C172.2, C173.2, C174.2, C175.2, C176.2, C177.2, C178.2, C179.2, C180.2, C181.2, C182.2, C183.2, C184.2, C185.2, C186.2, C187.2, C188.2, C189.2, C190.2, C191.2, C192.2, C1001.2, C1002.2, C1003.2, C1004.2, C1005.2, C1006.2, C1007.2, C1008.2, C1009.2, J2.1, J4.1, J6.1, Q1.3 (S), Q2.3 (S), Q3.3 (S), Q4.3 (S), Q5.3 (S), Q6.3 (S); also elsewhere on the board

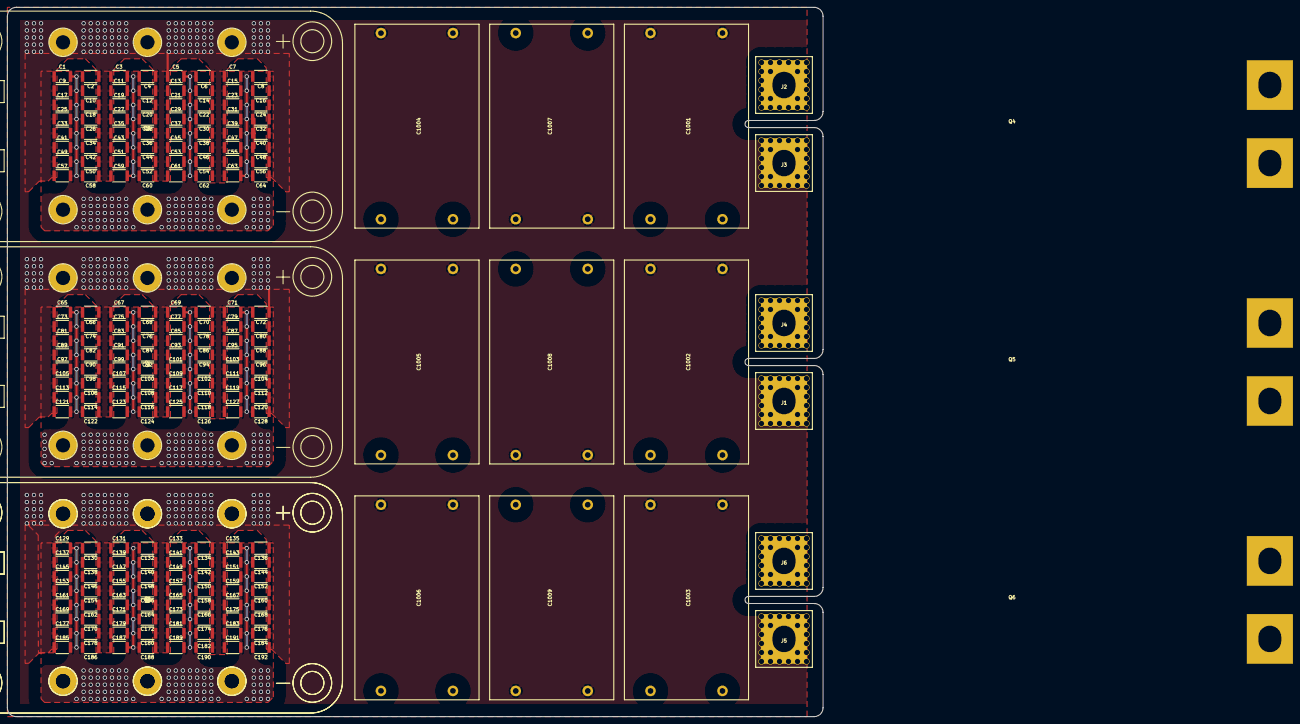
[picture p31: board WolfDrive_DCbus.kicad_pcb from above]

Board: 2 copper layers, 230.0 x 200.0 mm, 214 parts (0 on the bottom side), 2 nets.

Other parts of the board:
Q2#2: CAS325; CREE_CAS_PowerPins_DConly

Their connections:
/DC+: Q2#2.1; also elsewhere on the board
/DC-: Q2#2.3; also elsewhere on the board

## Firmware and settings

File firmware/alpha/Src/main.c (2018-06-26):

/**
  ******************************************************************************
  * @file           : main.c
  * @brief          : Main program body
  ******************************************************************************
  ** This notice applies to any and all portions of this file
  * that are not between comment pairs USER CODE BEGIN and
  * USER CODE END. Other portions of this file, whether 
  * inserted by the user or by software development tools
  * are owned by their respective copyright owners.
  *
  * COPYRIGHT(c) 2018 STMicroelectronics
  *
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
  ******************************************************************************
  */
/* Includes ------------------------------------------------------------------*/
#include "main.h"
#include "stm32h7xx_hal.h"
#include "string.h"

/* USER CODE BEGIN Includes */

#include "pwm.h"
#include "foc.h"
#include "math.h"
#include "pi.h"
#include "userparms.h"
#include "control.h"
#include "dac.h"

#include "stm32h7xx_hal_qspi.h"
/* USER CODE END Includes */

#if defined ( __ICCARM__ ) /*!< IAR Compiler */

#pragma location=0x30040000
ETH_DMADescTypeDef  DMARxDscrTab[ETH_RX_DESC_CNT]; /* Ethernet Rx DMA Descriptors */
#pragma location=0x30040060
ETH_DMADescTypeDef  DMATxDscrTab[ETH_TX_DESC_CNT]; /* Ethernet Tx DMA Descriptors */
#pragma location=0x30040200
uint8_t Rx_Buff[ETH_RX_DESC_CNT][ETH_MAX_PACKET_SIZE]; /* Ethernet Receive Buffers */

#elif defined ( __CC_ARM )  /* MDK ARM Compiler */

__attribute__((at(0x30040000))) ETH_DMADescTypeDef  DMARxDscrTab[ETH_RX_DESC_CNT]; /* Ethernet Rx DMA Descriptors */
__attribute__((at(0x30040060))) ETH_DMADescTypeDef  DMATxDscrTab[ETH_TX_DESC_CNT]; /* Ethernet Tx DMA Descriptors */
__attribute__((at(0x30040200))) uint8_t Rx_Buff[ETH_RX_DESC_CNT][ETH_MAX_PACKET_SIZE]; /* Ethernet Receive Buffer */

#elif defined ( __GNUC__ ) /* GNU Compiler */ 

ETH_DMADescTypeDef DMARxDscrTab[ETH_RX_DESC_CNT] __attribute__((section(".RxDecripSection"))); /* Ethernet Rx DMA Descriptors */
ETH_DMADescTypeDef DMATxDscrTab[ETH_TX_DESC_CNT] __attribute__((section(".TxDecripSection")));   /* Ethernet Tx DMA Descriptors */
uint8_t Rx_Buff[ETH_RX_DESC_CNT][ETH_MAX_PACKET_SIZE] __attribute__((section(".RxArraySection"))); /* Ethernet Receive Buffers */

#endif

ETH_TxPacketConfig TxConfig; 
ADC_HandleTypeDef hadc1;
ADC_HandleTypeDef hadc2;
ADC_HandleTypeDef hadc3;

ETH_HandleTypeDef heth;

QSPI_HandleTypeDef hqspi;

SD_HandleTypeDef hsd1;

SPI_HandleTypeDef hspi1;
SPI_HandleTypeDef hspi2;

TIM_HandleTypeDef htim1;

UART_HandleTypeDef huart3;
UART_HandleTypeDef huart6;

PCD_HandleTypeDef hpcd_USB_OTG_FS;

/* USER CODE BEGIN PV */
char buffer[50] = "Whatever.\n";
uint8_t SPI_Rx_Buf[6];
uint8_t qSPI_Rx_Buf[255];
tPIParm PIParmQ;
tPIParm PIParmD;
tCtrlParm CtrlParm;



/* USER CODE END PV */

void SystemClock_Config(void);
static void MX_GPIO_Init(void);
static void MX_ETH_Init(void);
static void MX_USART3_UART_Init(void);
static void MX_USB_OTG_FS_PCD_Init(void);
static void MX_ADC2_Init(void);
static void MX_ADC1_Init(void);
static void MX_SPI1_Init(void);
static void MX_QUADSPI_Init(void);
static void MX_TIM1_Init(void);
static void MX_SPI2_Init(void);
static void MX_ADC3_Init(void);
static void MX_USART6_UART_Init(void);
static void MX_SDMMC1_SD_Init(void);

void HAL_TIM_MspPostInit(TIM_HandleTypeDef* htim);
                                

/* USER CODE BEGIN PFP */
void InitUserParms(void);
void DoControl(void);
float ReadEncoder(SPI_HandleTypeDef hspi);
int32_t ReadEncoderInt(SPI_HandleTypeDef hspi);

HAL_StatusTypeDef     QSPI_Receive       (QSPI_HandleTypeDef *hqspi, uint8_t *pData, uint32_t Timeout);
//HAL_StatusTypeDef HAL_SPI_Receive2(SPI_HandleTypeDef *hspi, uint8_t *pData, uint16_t Size, uint32_t Timeout);
/* USER CODE END PFP */

/**
  * @brief  The application entry point.
  *
  * @retval None
  */
int main(void)
{
  /* MCU Configuration----------------------------------------------------------*/

  /* Reset of all peripherals, Initializes the Flash interface and the Systick. */
  HAL_Init();

  /* Configure the system clock */
  SystemClock_Config();

  /* Initialize all configured peripherals */
  MX_GPIO_Init();
  //MX_ETH_Init();
  MX_USART3_UART_Init();
  //MX_USB_OTG_FS_PCD_Init();
  //MX_ADC2_Init();
  //MX_ADC1_Init();
  MX_SPI1_Init();
  MX_QUADSPI_Init();
  MX_TIM1_Init();
  //MX_SPI2_Init();
  //MX_ADC3_Init();
  //MX_USART6_UART_Init();
  MX_DAC1_Init();
  //MX_SDMMC1_SD_Init();
  /* USER CODE BEGIN 2 */
  InitUserParms();

  pwm_test(htim1);
  set_duty(htim1, (uint32_t) 1250*1/4, 1);
  set_duty(htim1, (uint32_t) 1250*2/4, 2);
  set_duty(htim1, (uint32_t) 1250*3/4, 3);

  /*##-4- Enable DAC Channel1 and channel 2 ################################################*/
  if (HAL_DAC_Start(&hdac1, DAC_CHANNEL_1) != HAL_OK)
  {
    /* Start Error */
    Error_Handler();
  }
  if (HAL_DAC_Start(&hdac1, DAC_CHANNEL_2) != HAL_OK)
  {
    /* Start Error */
    Error_Handler();
  }

  QSPI_CommandTypeDef sCommand;
  sCommand.InstructionMode   = QSPI_INSTRUCTION_NONE;
  sCommand.AddressMode       = QSPI_ADDRESS_NONE;
  sCommand.Address           = ((uint32_t)0x0000);
  sCommand.AlternateByteMode = QSPI_ALTERNATE_BYTES_NONE;
  sCommand.DataMode          = QSPI_DATA_4_LINES;
  sCommand.DummyCycles       = 4;
  sCommand.NbData            = 16;
  sCommand.DdrMode           = QSPI_DDR_MODE_DISABLE;
  sCommand.DdrHoldHalfCycle  = QSPI_DDR_HHC_ANALOG_DELAY;
  sCommand.SIOOMode          = QSPI_SIOO_INST_ONLY_FIRST_CMD;

  if (HAL_QSPI_Command(&hqspi, &sCommand, 100) != HAL_OK)
  {
    _Error_Handler(__FILE__, __LINE__);
  }

  HAL_GPIO_WritePin(GPIOG, PWM_EN_Pin, GPIO_PIN_SET);
  //HAL_GPIO_WritePin(flt_reset_GPIO_Port,flt_reset_Pin, GPIO_PIN_SET);

  /* USER CODE END 2 */
  /* Infinite loop */
  /* USER CODE BEGIN WHILE */
  while (1)
  {
	  //HAL_GPIO_WritePin(GPIOB, GPIO_PIN_2|GPIO_PIN_10, GPIO_PIN_RESET);
	  //HAL_Delay(250);
	  //HAL_GPIO_WritePin(GPIOB, GPIO_PIN_2|GPIO_PIN_10, GPIO_PIN_SET);
	  //HAL_Delay(250);

	  /*
	  // Fake encoder
	  ParkParm.fAngle += 0.01f;
	  if(ParkParm.fAngle > 3.14159265f)
		  ParkParm.fAngle -= 6.28318531f;
	  // Fake ADC
	  ParkParm.fIa = 100*sin(0.2f+ParkParm.fAngle);
	  ParkParm.fIb = 100*sin(0.2f+ParkParm.fAngle+1.047f);
	  // Print*/
	  //sprintf(buffer,"angle,sin,cosine = %f,%f,%f \n",ParkParm.fAngle,ParkParm.fSin,ParkParm.fCos);
	  //HAL_UART_Transmit(&huart3, buffer, sizeof(buffer), HAL_MAX_DELAY);


	  /*theta_m += 0.062832f;
	  if (theta_m > 6.2832f)
		theta_m = 0;*/
	  //char buff[64] = "";
	  //sprintf(buff, "position=%.4f radians\n", theta_m);
	  //HAL_UART_Transmit(&huart3, buff, sizeof(buff), HAL_MAX_DELAY);


	  char dbuff[20] = "";
	  //sprintf(dbuff, "%u,%u,%f,%f,%f\n", Data1, Data2, ParkParm.fAngle, ParkParm.fSin, ParkParm.fCos);
	  sprintf(dbuff, "%f,%.2f\n", ParkParm.fAngle,CtrlParm.fVelE/diPoles/3.1416f*30.0f);
	  HAL_UART_Transmit(&huart3, dbuff, sizeof(dbuff), HAL_MAX_DELAY);

	  /* USER CODE END WHILE */

	  /* USER CODE BEGIN 3 */

  }
  /* USER CODE END 3 */

}

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
/* USER CODE BEGIN 4 */
void InitUserParms(void)
{
	// Setup required parameters

	// Pick scaling values to be 8 times nominal for speed and current

	// Use 8 times nominal mechanical speed of motor (in RPM) for scaling
	//MotorParm.iScaleMechRPM  = diNomRPM*8;

	// Number of pole pairs
	//MotorParm.iPoles        = diPoles ;

	// Encoder counts per revolution as detected by the
	//       dsPIC quadrature configuration.
	//MotorParm.iCntsPerRev  = diCntsPerRev;

	// Rotor time constant in sec
	//MotorParm.fRotorTmConst = dfRotorTmConst;

	// Basic loop period (in sec).  (PWM interrupt period)
	//MotorParm.fLoopPeriod = dLoopInTcy * dTcy;  //Loop period in cycles * sec/cycle

	// Encoder velocity interrupt period (in sec).
	//MotorParm.fVelIrpPeriod = MotorParm.fLoopPeriod;

	// Number of vel interrupts per velocity calculation.
	//MotorParm.iIrpPerCalc = diIrpPerCalc;       // In loops

	// Number of vel interrupts per velocity calculation.
	//MotorParm.iIrpPerPos = diIrpPerPos;       // In loops

	// Scale mechanical speed of motor (in rev/sec)
	//MotorParm.fScaleMechRPS = MotorParm.iScaleMechRPM/60.0;

	// Scaled flux speed of motor (in rev/sec)
	// All dimensionless flux velocities scaled by this value.
	//MotorParm.fScaleFluxRPS = MotorParm.iPoles*MotorParm.fScaleMechRPS;

	// Minimum period of one revolution of flux vector (in sec)
	//MotorParm.fScaleFluxPeriod = 1.0/MotorParm.fScaleFluxRPS;

	// Fraction of revolution per LoopTime at maximum flux velocity
	//MotorParm.fScaleFracRevPerLoop = MotorParm.fLoopPeriod * MotorParm.fScaleFluxRPS;

	// Scaled flux speed of motor (in radians/sec)
	// All dimensionless velocities in radians/sec scaled by this value.
	//MotorParm.fScaleFluxSpeed = 6.283 * MotorParm.fScaleFluxRPS;

	// scaled mech. speed of motor in rad/s

	// Encoder count rate at iScaleMechRPM
	//MotorParm.lScaleCntRate = MotorParm.iCntsPerRev * (MotorParm.iScaleMechRPM/60.0);



	// ============= Open Loop ======================

	//    OpenLoopParm.qKdelta = 32768.0 * 2 * MotorParm.iPoles * MotorParm.fLoopPeriod * MotorParm.fScaleMechRPS;
	//    OpenLoopParm.qVelMech = dqOL_VelMech;
	//    CtrlParm.qVelRef = OpenLoopParm.qVelMech;
	/*
            InitOpenLoop();

        // ============= Field Weakening ===============
        // Field Weakening constant for constant torque range
            FdWeakParm.qK1 = dqK1;       // Flux reference value
	 */
	// ============= PI D Term ===============
	PIParmD.fKp = dDqKp;
	PIParmD.fKi = dDqKi;
	PIParmD.fKc = dDqKc;
	PIParmD.fOutMax = dDqOutMax;
	PIParmD.fOutMin = -PIParmD.fOutMax;

	InitPI(&PIParmD);

	// ============= PI Q Term ===============
	PIParmQ.fKp = dQqKp;
	PIParmQ.fKi = dQqKi;
	PIParmQ.fKc = dQqKc;
	PIParmQ.fOutMax = dQqOutMax;
	PIParmQ.fOutMin = -PIParmQ.fOutMax;

	InitPI(&PIParmQ);

	// ============= ADC - Measure Current & Pot ======================

	// Scaling constants: Determined by calibration or hardware design.
	//ReadADCParm.qK      = dqK;

	//MeasCurrParm.qKa    = dqKa;
	//MeasCurrParm.qKb    = dqKb;
	// Appcon/Changes 25 Jan 2007
	/*
    MeasCurrParm.iOffsetCompVelLimit= iCompVelLimitLow;
    MeasCurrParm.iOffsetCompHyst=iCompVelHyst;
    MeasCurrParm.iOffsetCompAktiv=0;
        CtrlParm.qVelRef=0;     // Speed reference value
	 */
	//*******************************

	// Inital offsets
	//InitMeasCompCurr( 3339, 3225 );  // 564, 563 if encoder not connected so (564-2^9)*2^6, measured 1.80v offset on scope with 50mv/div precision at 3.24V aVDD .. center at 1.62V, so 0.18V offset,

}

void DoControl(void)
{
	// Closed Loop Vector Control

	/*position = read_encoder()-theta_qoffset;				// offset measured with rotor flux aligned to q, 0 rad=0, pi rad=2^15 so INTEGER not Q scaling

	ParkParm.fAngle = (position+timing_angle)*diPoles;		// pass park electrical position, so multiply by pole pairs
	EncoderParm.iCurrCnt = ((unsigned short)position)>>1;	// pass mechanical position to CalcVel sub.
	*/

	// PI control to test ADC, set Ia=VdRef

	/*PIParmD.fInMeas = ParkParm.fId;
	        PIParmD.fInRef  = CtrlParm.fVdRef;
	        CalcPI(&PIParmD);
	        ParkParm.fVd    = PIParmD.fOut;
	 */

	// PI control for Q
	PIParmQ.fInMeas = ParkParm.fIq;
	PIParmQ.fInRef  = CtrlParm.fVqRef;
	CalcPI(&PIParmQ);
	// Calc. feed forward terms
	/*
	emf=((long)EncoderParm.fVelMech*dqEmfScale);
	ir=((long)CtrlParm.fVqRef*dqRsScale);
	ff=PIParmQ.qOut+emf+ir;
	if( ff > PIParmQ.fOutMax )
		ParkParm.fVq = PIParmQ.fOutMax;
	else if( ff < PIParmQ.qOutMin )
		ParkParm.fVq = PIParmQ.fOutMin;
	else
		ParkParm.fVq = ff;*/
	ParkParm.fVq=PIParmQ.fOut;

	// PI control for D
	PIParmD.fInMeas = ParkParm.fId;
	PIParmD.fInRef  = CtrlParm.fVdRef;
	CalcPI(&PIParmD);
	ParkParm.fVd    = PIParmD.fOut;
}

float ReadEncoder(SPI_HandleTypeDef hspi)
{
	if (HAL_SPI_Receive(&hspi, (uint8_t *)SPI_Rx_Buf, 6, 2) != HAL_OK)
		_Error_Handler(__FILE__, __LINE__);
	/*char buf[64], *pos = buf;
	  for (int i = 0 ; i != 6 ; i++) {
	      if (i) {
	          pos += sprintf(pos, ", ");
	      }
	      pos += sprintf(pos, "%d", SPI_Rx_Buf[i]);
	  }
	  sprintf(buf, "%s\n", buf);
	  HAL_UART_Transmit(&huart3, buf, sizeof(buf), HAL_MAX_DELAY);*/
	uint32_t posi = 0;
	//posi = ((uint32_t)SPI_Rx_Buf[2]) << 24 | ((uint32_t)SPI_Rx_Buf[3]) << 16 | ((uint32_t)SPI_Rx_Buf[4]) << 8;
	//posi &= 0xFFFFF000;	// Encoder is 20b resolution
	// AkSIM v1 has 12b ACK
	//posi = ((uint32_t)SPI_Rx_Buf[2]) << 12 | ((uint32_t)SPI_Rx_Buf[3]) << 4 | ((uint32_t)SPI_Rx_Buf[4]) >> 4;
	// AkSim v2 has 13b ACK
	posi = ((uint32_t)SPI_Rx_Buf[2]) << 13 | ((uint32_t)SPI_Rx_Buf[3]) << 5 | ((uint32_t)SPI_Rx_Buf[4]) >> 3;
	float f_posi = ((float)posi)/0xFFFFF*360;
	return f_posi;
}

int32_t ReadEncoderInt(SPI_HandleTypeDef hspi)
{
	// ****AKSIM 1 ONLY****
	if (HAL_SPI_Receive(&hspi, (uint8_t *)SPI_Rx_Buf, 6, 2) != HAL_OK)
		_Error_Handler(__FILE__, __LINE__);
	/*char buf[64], *pos = buf;
	  for (int i = 0 ; i != 6 ; i++) {
	      if (i) {
	          pos += sprintf(pos, ", ");
	      }
	      pos += sprintf(pos, "%d", SPI_Rx_Buf[i]);
	  }
	  sprintf(buf, "%s\n", buf);
	  HAL_UART_Transmit(&huart3, buf, sizeof(buf), HAL_MAX_DELAY);*/
	uint32_t posi = 0;
	// ****AKSIM 1 ONLY****
	posi = ((uint32_t)SPI_Rx_Buf[2]) << 24 | ((uint32_t)SPI_Rx_Buf[3]) << 16 | ((uint32_t)SPI_Rx_Buf[4]) << 8;
	posi &= 0xFFFFF000;	// Encoder is 20b resolution
	//posi = ((uint32_t)SPI_Rx_Buf[2]) << 12 | ((uint32_t)SPI_Rx_Buf[3]) << 4 | ((uint32_t)SPI_Rx_Buf[4]) >> 4;
	//float f_posi = ((float)posi)/0xFFFFF*360;
	//return f_posi;
	return (int32_t)(posi-0x7FFFFFF);
}

void ReadQSPI(QSPI_HandleTypeDef *hqspi)
{
	  if (QSPI_Receive(&hqspi, (uint8_t *)qSPI_Rx_Buf, 100) != HAL_OK)
		  _Error_Handler(__FILE__, __LINE__);

	  /*char buf[128] = "", *pos = buf;
	  for (int i = 0 ; i != 16 ; i++) {
		  if (i) {
			  pos += sprintf(pos, ", ");
		  }
		  pos += sprintf(pos, "%x", qSPI_Rx_Buf[i]);
	  }
	  sprintf(buf, "%s\n", buf);
	  HAL_UART_Transmit(&huart3, buf, sizeof(buf), HAL_MAX_DELAY);*/

	  uint8_t twobits[16];
	  uint32_t iobyte[4];

	  for (int by = 0 ; by != 4; by++) {
		  iobyte[by] = 0; // comment out to test comms, OR all and data check for 0xfffcfffc
		  for (uint8_t bi = 0 ; bi != 16; bi++) {
			  twobits[bi] = ((qSPI_Rx_Buf[bi] >> by) & 1) | ((qSPI_Rx_Buf[bi] >> (by+3)) & 2);
			  iobyte[by] |= twobits[bi] << ((15-bi) << 1);
		  }
		  //io0byte[by] = twobits[0] | (twobits[1] << 2) | (twobits[2] << 4) | (twobits[3] << 6);
	  }

	  int16_t extADC[8];
	  for (int ch = 0; ch !=4; ch++) {
		  extADC[ch+ch] = (uint16_t)(iobyte[ch] & 0xFFFC); // [13:0][xx]
		  extADC[ch+ch+1] = (uint16_t)((iobyte[ch] >> 16) & 0xFFFC);
	  }

	  char buff[128] = "";
	  //sprintf(buff, "%x,%x,%x,%x\n", iobyte[0],iobyte[1],iobyte[2],iobyte[3]);
	  //sprintf(buff, "%x,%x,%x,%x,%x,%x\n", iobyte[0],iobyte[1],extADC[0],extADC[1],extADC[2],extADC[3]);
	  //sprintf(buff, "%d,%d,%d,%d\n",extADC[0],extADC[1],extADC[2],extADC[3]);

	  float Vdc = (float)((uint16_t)extADC[3])*0.012f;
	  float offset = -1.215f;
	  float I = ((float)(extADC[1]))/0x7FFF*1250-offset;
	  //sprintf(buff, "%.1f,%.3f\n", Vdc,I);
	  //HAL_UART_Transmit(&huart3, buff, sizeof(buff), HAL_MAX_DELAY);

	  /*uint8_t fi2b = ((qSPI_Rx_Buf[0] >> 1) & 1) | ((qSPI_Rx_Buf[0] >> 4) & 2);
	  uint8_t se2b = ((qSPI_Rx_Buf[1] >> 1) & 1) | ((qSPI_Rx_Buf[1] >> 4) & 2);
	  uint8_t th2b = ((qSPI_Rx_Buf[2] >> 1) & 1) | ((qSPI_Rx_Buf[2] >> 4) & 2);
	  uint8_t fo2b = ((qSPI_Rx_Buf[3] >> 1) & 1) | ((qSPI_Rx_Buf[3] >> 4) & 2);
	  uint8_t io1 = fi2b | (se2b << 2) | (th2b << 4) | (fo2b << 6);
	  char bufff[128] = "";
	  sprintf(bufff, "%x,%x,%x,%x = %x\n", fi2b, se2b, th2b, fo2b, io1);
	  HAL_UART_Transmit(&huart3, bufff, sizeof(bufff), HAL_MAX_DELAY);*/
}

static HAL_StatusTypeDef QSPI_WaitFlagStateUntilTimeout(QSPI_HandleTypeDef *hqspi, uint32_t Flag,
                                                        FlagStatus State, uint32_t tickstart, uint32_t Timeout)
{
  /* Wait until flag is in expected state */
  while((FlagStatus)(__HAL_QSPI_GET_FLAG(hqspi, Flag)) != State)
  {
    /* Check for the Timeout */
    if (Timeout != HAL_MAX_DELAY)
    {
      if((Timeout == 0) || ((HAL_GetTick() - tickstart) > Timeout))
      {
        hqspi->State     = HAL_QSPI_STATE_ERROR;
        hqspi->ErrorCode |= HAL_QSPI_ERROR_TIMEOUT;

        return HAL_ERROR;
      }
    }
  }
  return HAL_OK;
}


HAL_StatusTypeDef QSPI_Receive(QSPI_HandleTypeDef *hqspi, uint8_t *pData, uint32_t Timeout)
{
	HAL_StatusTypeDef status = HAL_OK;
	uint32_t tickstart = HAL_GetTick();
	uint32_t addr_reg = READ_REG(hqspi->Instance->AR);
	__IO uint32_t *data_reg = &hqspi->Instance->DR;

	/* Process locked */
	__HAL_LOCK(hqspi);

	if(hqspi->State == HAL_QSPI_STATE_READY)
	{
		hqspi->ErrorCode = HAL_QSPI_ERROR_NONE;

		if(pData != NULL )
		{
			/* Update state */
			hqspi->State = HAL_QSPI_STATE_BUSY_INDIRECT_RX;

			/* Configure counters and size of the handle */
			hqspi->RxXferCount = READ_REG(hqspi->Instance->DLR) + 10;
			hqspi->RxXferSize = READ_REG(hqspi->Instance->DLR) + 10;
			hqspi->pRxBuffPtr = pData;

			/* Configure QSPI: CCR register with functional as indirect read */
			MODIFY_REG(hqspi->Instance->CCR, QUADSPI_CCR_FMODE, ((uint32_t)QUADSPI_CCR_FMODE_0));
			///* Start the transfer by re-writing the address in AR register */
			//WRITE_REG(hqspi->Instance->AR, addr_reg);
		    /* Start the transfer by writing the address CCR register */
		    __IO uint32_t *data_reg = &hqspi->Instance->DR;
		    MODIFY_REG(hqspi->Instance->CCR, QUADSPI_CCR_INSTRUCTION, 0x03);

			while(hqspi->RxXferCount > 0)
			{
				/* Wait until FT or TC flag is set to read received data */
				status = QSPI_WaitFlagStateUntilTimeout(hqspi, (QSPI_FLAG_FT | QSPI_FLAG_TC), SET, tickstart, Timeout);

				if  (status != HAL_OK)
				{
					break;
				}

				*hqspi->pRxBuffPtr++ = *(__IO uint8_t *)data_reg;
				hqspi->RxXferCount--;
			}

			if (status == HAL_OK)
			{
				/* Wait until TC flag is set to go back in idle state */
				status = QSPI_WaitFlagStateUntilTimeout(hqspi, QSPI_FLAG_TC, SET, tickstart, Timeout);

				if  (status == HAL_OK)
				{
					/* Clear Transfer Complete bit */
					__HAL_QSPI_CLEAR_FLAG(hqspi, QSPI_FLAG_TC);
				}
			}

			/* Update QSPI state */
			hqspi->State = HAL_QSPI_STATE_READY;
		}
		else
		{
			hqspi->ErrorCode |= HAL_QSPI_ERROR_INVALID_PARAM;
			status = HAL_ERROR;
		}
	}
	else
	{
		status = HAL_BUSY;
	}

	/* Process unlocked */
	__HAL_UNLOCK(hqspi);

	return status;
}

/* USER CODE END 4 */
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


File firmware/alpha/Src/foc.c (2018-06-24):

#include "stdint.h"
#include "main.h"
#include "stm32h7xx_hal.h"
#include "foc.h"
//#include "pwm.h"
//#include "math.h"
//#include "arm_math.h"

void SinCos(void)
{
	//arm_sin_cos_f32(Angle, &sinA, &cosA); // uses degrees, not faster?
	//ParkParm.fSin = arm_sin_f32(ParkParm.fAngle);
	//ParkParm.fCos = arm_cos_f32(ParkParm.fAngle);
	//ParkParm.fSin = sin(ParkParm.fAngle);
	//ParkParm.fCos = cos(ParkParm.fAngle);

	// Algorithm from http://lab.polygonal.de/2007/07/18/fast-and-accurate-sinecosine-approximation/
	float angle = ParkParm.fAngle;

	//always wrap input angle to -PI..PI
	if (angle < -3.14159265f)
		angle += 6.28318531f;
	else if (angle >  3.14159265f)
		angle -= 6.28318531f;

	//compute sine
	if (angle < 0)
	{
		ParkParm.fSin = 1.27323954f * angle + .405284735f * angle * angle;

		if (ParkParm.fSin < 0)
			ParkParm.fSin = .225f * (ParkParm.fSin *-ParkParm.fSin - ParkParm.fSin) + ParkParm.fSin;
		else
			ParkParm.fSin = .225f * (ParkParm.fSin * ParkParm.fSin - ParkParm.fSin) + ParkParm.fSin;
	}
	else
	{
		ParkParm.fSin = 1.27323954f * angle - 0.405284735f * angle * angle;

		if (ParkParm.fSin < 0)
			ParkParm.fSin = .225f * (ParkParm.fSin *-ParkParm.fSin - ParkParm.fSin) + ParkParm.fSin;
		else
			ParkParm.fSin = .225f * (ParkParm.fSin * ParkParm.fSin - ParkParm.fSin) + ParkParm.fSin;
	}

	//compute cosine: sin(angle + PI/2) = cos(angle)
	angle += 1.57079632f;
	if (angle >  3.14159265f)
		angle -= 6.28318531f;

	if (angle < 0)
	{
		ParkParm.fCos = 1.27323954f * angle + 0.405284735f * angle * angle;

		if (ParkParm.fCos < 0)
			ParkParm.fCos = .225f * (ParkParm.fCos *-ParkParm.fCos - ParkParm.fCos) + ParkParm.fCos;
		else
			ParkParm.fCos = .225f * (ParkParm.fCos * ParkParm.fCos - ParkParm.fCos) + ParkParm.fCos;
	}
	else
	{
		ParkParm.fCos = 1.27323954f * angle - 0.405284735f * angle * angle;

		if (ParkParm.fCos < 0)
			ParkParm.fCos = .225f * (ParkParm.fCos *-ParkParm.fCos - ParkParm.fCos) + ParkParm.fCos;
		else
			ParkParm.fCos = .225f * (ParkParm.fCos * ParkParm.fCos - ParkParm.fCos) + ParkParm.fCos;
	}
}

void ClarkePark(void)
{
	// Assumes the Cos an Sin values are in ParkParm.fSin, ParkParm.fCos
	ParkParm.fIalpha = ParkParm.fIa;
	ParkParm.fIbeta = (ParkParm.fIa + 2.0f * ParkParm.fIb) * 0.577350269f;

	//where sum(In)=0;
	ParkParm.fId =  ParkParm.fIalpha*ParkParm.fCos + ParkParm.fIbeta*ParkParm.fSin;
	ParkParm.fIq = -ParkParm.fIalpha*ParkParm.fSin + ParkParm.fIbeta*ParkParm.fCos;
}

void InvPark(void)
{
	// Calculate Valpha, Vbeta from Sin, Cos, Vd, Vq
	// Assumes the Cos an Sin values are in ParkParm.fSin, ParkParm.fCos
	ParkParm.fValpha = ParkParm.fVd*ParkParm.fCos - ParkParm.fVq*ParkParm.fSin;
	ParkParm.fVbeta  = ParkParm.fVd*ParkParm.fSin + ParkParm.fVq*ParkParm.fCos;

}

void CalcRefVec(void)
{
	// Calculate Vr{1,2,3} from Valpha, Vbeta
	ParkParm.fV1 =  ParkParm.fVbeta;
	ParkParm.fV2 = -ParkParm.fVbeta/2 + 0.86602540378444f * ParkParm.fValpha;
	ParkParm.fV3 = -ParkParm.fVbeta/2 + 1.22474487139159f * ParkParm.fValpha;
}

void CalcSVGen(TIM_HandleTypeDef htim1)
{
	float dPWM1 = 0;
	float dPWM2 = 0;
	float dPWM3 = 0;

	if( ParkParm.fV1 >= 0 )
	{
		// (xx1)
		if( ParkParm.fV2 >= 0 )
		{
			// (x11)
			// Must be Sector 3 since Sector 7 not allowed
			// Sector 3: (0,1,1)  0-60 degrees
			SVMParm.fT1 = ParkParm.fV2;
			SVMParm.fT2 = ParkParm.fV1;
			CalcTimes();
			dPWM1 = SVMParm.fTa;
			dPWM2 = SVMParm.fTb;
			dPWM3 = SVMParm.fTc;
		}
		else
		{
			// (x01)
			if( ParkParm.fV3 >= 0 )
			{
				// Sector 5: (1,0,1)  120-180 degrees
				SVMParm.fT1 = ParkParm.fV1;
				SVMParm.fT2 = ParkParm.fV3;
				CalcTimes();
				dPWM1 = SVMParm.fTc;
				dPWM2 = SVMParm.fTa;
				dPWM3 = SVMParm.fTb;

			}
			else
			{
				// Sector 1: (0,0,1)  60-120 degrees
				SVMParm.fT1 = -ParkParm.fV2;
				SVMParm.fT2 = -ParkParm.fV3;
				CalcTimes();
				dPWM1 = SVMParm.fTb;
				dPWM2 = SVMParm.fTa;
				dPWM3 = SVMParm.fTc;
			}
		}
	}
	else
	{
		// (xx0)
		if( ParkParm.fV2 >= 0 )
		{
			// (x10)
			if( ParkParm.fV3 >= 0 )
			{
				// Sector 6: (1,1,0)  240-300 degrees
				SVMParm.fT1 = ParkParm.fV3;
				SVMParm.fT2 = ParkParm.fV2;
				CalcTimes();
				dPWM1 = SVMParm.fTb;
				dPWM2 = SVMParm.fTc;
				dPWM3 = SVMParm.fTa;
			}
			else
			{
				// Sector 2: (0,1,0)  300-0 degrees
				SVMParm.fT1 = -ParkParm.fV3;
				SVMParm.fT2 = -ParkParm.fV1;
				CalcTimes();
				dPWM1 = SVMParm.fTa;
				dPWM2 = SVMParm.fTc;
				dPWM3 = SVMParm.fTb;
			}
		}
		else
		{
			// (x00)
			// Must be Sector 4 since Sector 0 not allowed
			// Sector 4: (1,0,0)  180-240 degrees
			SVMParm.fT1 = -ParkParm.fV1;
			SVMParm.fT2 = -ParkParm.fV2;
			CalcTimes();
			dPWM1 = SVMParm.fTc;
			dPWM2 = SVMParm.fTb;
			dPWM3 = SVMParm.fTa;
		}
	}
	//set_duty(htim1, dPWM1, 1);
	//set_duty(htim1, dPWM2, 2);
	//set_duty(htim1, dPWM3, 3);
	//__HAL_TIM_SET_COMPARE(&htim1, TIM_CHANNEL_1, dPWM1);
	//__HAL_TIM_SET_COMPARE(&htim1, TIM_CHANNEL_2, dPWM2);
	//__HAL_TIM_SET_COMPARE(&htim1, TIM_CHANNEL_3, dPWM3);
}

void CalcTimes(void)
{
	uint32_t PWM = SVMParm.iPWMPeriod;
	SVMParm.fT1 = PWM*SVMParm.fT1;
	SVMParm.fT2 = PWM*SVMParm.fT2;
	SVMParm.fTc = (PWM-SVMParm.fT1-SVMParm.fT2)/2;
	SVMParm.fTb = SVMParm.fTc + SVMParm.fT1;
	SVMParm.fTa = SVMParm.fTb + SVMParm.fT2;
}

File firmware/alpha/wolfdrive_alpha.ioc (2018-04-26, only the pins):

Mcu.UserName=STM32H743ZITx
PA0-WKUP.GPIO_Label=temp_motor
PA0-WKUP.Signal=ADC1_INP16
PA1.GPIO_Label=RMII_REF_CLK
PA1.Signal=ETH_REF_CLK
PA10.GPIO_Label=USB_ID
PA10.Signal=USB_OTG_FS_ID
PA11.GPIO_Label=USB_DM
PA11.Signal=USB_OTG_FS_DM
PA12.GPIO_Label=USB_DP
PA12.Signal=USB_OTG_FS_DP
PA13.GPIO_Label=TMS
PA13.Signal=SYS_JTMS-SWDIO
PA14.GPIO_Label=TCK
PA14.Signal=SYS_JTCK-SWCLK
PA15.Signal=SPI1_NSS
PA2.GPIO_Label=RMII_MDIO
PA2.Signal=ETH_MDIO
PA3.GPIO_Label=RTD_A
PA3.Signal=ADCx_INP15
PA4.GPIO_Label=RTD_C
PA4.Signal=ADCx_INP18
PA5.Signal=SPI1_SCK
PA6.Signal=SPI1_MISO
PA7.GPIO_Label=RMII_CRS_DV
PA7.Signal=ETH_CRS_DV
PA8.GPIO_Label=USB_SOF [TP1]
PA8.Signal=USB_OTG_FS_SOF
PA9.GPIO_Label=USB_VBUS
PA9.Signal=USB_OTG_FS_VBUS
PB0.GPIO_Label=LD1 [Green]
PB0.Signal=GPIO_Output
PB1.GPIO_Label=ADC_throttle
PB1.Signal=ADCx_INP5
PB10.Signal=QUADSPI_BK1_NCS
PB11.GPIO_Label=run_switch
PB11.Signal=GPIO_Input
PB12.GPIO_Label=run_LED
PB12.Signal=GPIO_Output
PB13.GPIO_Label=RMII_TXD1
PB13.Signal=ETH_TXD1
PB14.GPIO_Label=LD3 [Red]
PB14.Signal=GPIO_Output
PB15.Signal=SPI2_MOSI
PB2.Signal=QUADSPI_CLK
PB3.GPIO_Label=SWO
PB3.Signal=SYS_JTDO-SWO
PB4.Signal=SPI2_NSS
PB5.Signal=SPI1_MOSI
PB7.GPIO_Label=LD2 [Blue]
PB7.Signal=GPIO_Output
PC0.GPIO_Label=RTD_B
PC0.Signal=ADCx_INP10
PC1.GPIO_Label=RMII_MDC
PC1.Signal=ETH_MDC
PC10.Signal=SDMMC1_D2
PC11.Signal=SDMMC1_D3
PC12.Signal=SDMMC1_CK
PC13.GPIO_Label=B1 [user]
PC13.Signal=GPIO_Input
PC14-OSC32_IN.Signal=RCC_OSC32_IN
PC15-OSC32_OUT.Signal=RCC_OSC32_OUT
PC2_C.Signal=SPI2_MISO
PC3_C.GPIO_Label=temp_motor
PC3_C.Signal=ADC3_INP1
PC4.GPIO_Label=RMII_RXD0
PC4.Signal=ETH_RXD0
PC5.GPIO_Label=RMII_RXD1
PC5.Signal=ETH_RXD1
PC8.Signal=SDMMC1_D0
PC9.Signal=SDMMC1_D1
PD11.Signal=QUADSPI_BK1_IO0
PD12.Signal=QUADSPI_BK1_IO1
PD13.Signal=QUADSPI_BK1_IO3
PD2.Signal=SDMMC1_CMD
PD3.Signal=SPI2_SCK
PD8.GPIO_Label=STLK_RX [STM32F103CBT6_PA3]
PD8.Signal=USART3_TX
PD9.GPIO_Label=STLK_TX [STM32F103CBT6_PA2]
PD9.Signal=USART3_RX
PE10.Signal=TIM1_CH2N
PE11.Signal=S_TIM1_CH2
PE12.Signal=TIM1_CH3N
PE13.Signal=S_TIM1_CH3
PE14.GPIO_Label=up_switch
PE14.Signal=GPIO_Input
PE15.GPIO_Label=down_switch
PE15.Signal=GPIO_Input
PE2.Signal=QUADSPI_BK1_IO2
PE4.GPIO_Label=flt_status
PE4.Signal=GPIO_Input
PE7.GPIO_Label=limit_torque
PE7.Signal=GPIO_Input
PE8.Signal=TIM1_CH1N
PE9.Signal=S_TIM1_CH1
PF12.GPIO_Label=reverse
PF12.Signal=GPIO_Input
PF13.GPIO_Label=flt_overIV
PF13.Signal=GPXTI13
PF14.GPIO_Label=flt_gate
PF14.Signal=GPXTI14
PF15.GPIO_Label=flt_reset
PF15.Signal=GPIO_Output
PF3.GPIO_Label=temp_coolant
PF3.Signal=ADC3_INP5
PG0.GPIO_Label=PWM_EN
PG0.Signal=GPIO_Output
PG1.GPIO_Label=contactor
PG1.Signal=GPIO_Output
PG11.GPIO_Label=RMII_TX_EN
PG11.Signal=ETH_TX_EN
PG13.GPIO_Label=RMII_TXD0
PG13.Signal=ETH_TXD0
PG14.Signal=USART6_TX
PG2.GPIO_Label=cont_aux
PG2.Signal=GPIO_Input
PG3.GPIO_Label=Estop
PG3.Signal=GPXTI3
PG6.GPIO_Label=USB_PowerSwitchOn [STMPS2151STR_EN]
PG6.Signal=GPIO_Output
PG7.GPIO_Label=USB_OverCurrent [STMPS2151STR_FAULT]
PG7.Signal=GPIO_Input
PG9.Signal=USART6_RX
PH0-OSC_IN.GPIO_Label=MCO
PH0-OSC_IN.Signal=RCC_OSC_IN
PH1-OSC_OUT.Signal=RCC_OSC_OUT

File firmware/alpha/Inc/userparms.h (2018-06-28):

 /**********************************************************************
 *                                                                     *
 *                        Software License Agreement                   *
 *                                                                     *
 *    The software supplied herewith by Microchip Technology           *
 *    Incorporated (the "Company") for its dsPIC controller            *
 *    is intended and supplied to you, the Company's customer,         *
 *    for use solely and exclusively on Microchip dsPIC                *
 *    products. The software is owned by the Company and/or its        *
 *    supplier, and is protected under applicable copyright laws. All  *
 *    rights are reserved. Any use in violation of the foregoing       *
 *    restrictions may subject the user to criminal sanctions under    *
 *    applicable laws, as well as to civil liability for the breach of *
 *    the terms and conditions of this license.                        *
 *                                                                     *
 *    THIS SOFTWARE IS PROVIDED IN AN "AS IS" CONDITION.  NO           *
 *    WARRANTIES, WHETHER EXPRESS, IMPLIED OR STATUTORY, INCLUDING,    *
 *    BUT NOT LIMITED TO, IMPLIED WARRANTIES OF MERCHANTABILITY AND    *
 *    FITNESS FOR A PARTICULAR PURPOSE APPLY TO THIS SOFTWARE. THE     *
 *    COMPANY SHALL NOT, IN ANY CIRCUMSTANCES, BE LIABLE FOR SPECIAL,  *
 *    INCIDENTAL OR CONSEQUENTIAL DAMAGES, FOR ANY REASON WHATSOEVER.  *
 *                                                                     *
  **********************************************************************/



// This is a macro used to convert a floating point value to a
// fixed point fractional value.
/* if already defined in dsp.h do not define here
#define X) \
   ((X < 0.0) ? (int)(32768*(X) - 0.5) : (int)(32767*(X) + 0.5)) ;
*/
//**************  Oscillator **************

#define dLoopTimeInSec  0.00004f         	// PWM Period - 40 uSec, 25Khz PWM
#define dPWMfreq		(1/dLoopTimeInSec) 	// PWM frequency (Hz)
#define dDeadTimeSec    0.0000005        	// Deadtime in seconds ## NOT IMPLEMENTED ##
//#define	dDispLoopTime	0.100			// Display and button polling loop period in sec

// Derived
#define dFosc       	400000000            	// Clock frequency (Hz)
#define dFcy        	400000000            	// Instruction cycle frequency (Hz)
#define dTcy        	(1.0/dFcy)          	// Instruction cycle period (sec)
#define dFClkDeadTime 	200000000
#define dDeadTime   	(int)(dDeadTimeSec*dFClkDeadTime) // Dead time in dTcys

#define dLoopInTcy  	(dLoopTimeInSec/dTcy)   // Basic loop period in units of Tcy

//**************  Motor Parameters **************
#define diPoles         8       // Number of pole pairs
//#define diCntsPerRev    32768    // Encoder counts per revolution
//#define diNomRPM        8000    // Name Plate Motor RPM

#define dqTorqueConst   0.644     // Motor back-emf constant in V/rad/s
//#define diDCBusV        64      // volts

//#define dqEmfScale      0.54)//diNomRPM*8/60*2*3.14159/diDCBusV/64*0.71)  //NomRPM*8/60*2 pi/DVBusV/2^6 * dqTorqueConst
//#define dqRsScale       0.830  //

//************** Open Loop **************
//#define dqOL_VelMech    0.00805    // 900/7=128.6 rpm for test

//************** Measurement **************
//#define diIrpPerCalc    5       // PWM loops per velocity calculation
//#define diIrpPerPos     4       // Vel. loops per position calculation

//#define diIrpPerData    200      // 200/20khz=10ms sample f
//#define diIrpPerSignal  2000   // 1s sample f
//************** PI Coefficients **************

// This definition can be used to bypass the velocity control loop.
// If TORQUE_MODE is defined, speed demand value
// is passed directly to the Q (torque) control loop.
//#define	TORQUE_MODE

//******** D Control Loop Coefficients *******
#define     dDqKp           0.05f;     //
#define     dDqKi           0.03f;     //
#define     dDqKc           0.03f;     //
#define     dDqOutMax       0.7071f;   //

//******** Q Control Loop Coefficients *******
#define     dQqKp           0.05f;     // 0.06
#define     dQqKi           0.03f;     // 0.002
#define     dQqKc           0.03f;     // 0.002
#define     dQqOutMax       0.7071f;   // 0.7071

//*** Velocity Control Loop Coefficients *****
/*#define     dQrefqKp        0.05f;     // 0.4
#define     dQrefqKi        0.005f;    // 0.02
#define     dQrefqKc        0.005f;    // 0.02
#define     dQrefqOutMax    0.448f;    // 0.448
*/
//*** Position Control Loop Coefficients *****
/*#define     dPrefqKp        0.004f;    // 0.375
#define     dPrefqKi        0.05f;     //
#define     dPrefqKc        0.05f;     //
#define     dPrefqOutMax    0.15f;     //0.024
*/
//************** ADC Scaling **************
// Scaling constants: Determined by calibration or hardware design.

#define     dqK             1.0f;     // !!!!!!
#define     dqKa            1.0f;     // ADC Ia current scale factor
#define     dqKb            1.0f;     // ADC Ib current scale factor
#define     dqKc            1.0f;     // ADC Ic current scale factor

//************** Field Weakening **************
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

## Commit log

2018-03-06 Initial commit - untested
    [Cree_CAS325_DCholes.dxf, Cree_CAS325_outline.dxf, Cree_CAS325_outline_DXF04.dxf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]
2018-03-08 Housekeeping, missed label dxf added
    [WolfDrive_H7Controller-F.SilkS.dxf, WolfDrive_H7_pinassignment.ods, testpoint_labels.dxf]
2018-03-08 .gitignore is now working
    [Edge.Cuts.dxf, WolfDrive_H7Controller-Edge.Cuts.dxf, WolfDrive_H7Controller-F.SilkS.dxf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]
2018-03-12 Added extra SPI to pin assignment, combine with QSPI
2018-03-13 added missing testpoint labels to silk
    [WolfDrive_H7Controller-B.Cu.gbr, WolfDrive_H7Controller-B.Mask.gbr, WolfDrive_H7Controller-B.SilkS.gbr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]
2018-03-13 grounded test on FT232RL, issue #2
    [WolfDrive_H7Controller.sch]
2018-03-14 work towards fixing v0.1 issues, 1-5
    [WolfDrive_H7Controller.sch]
2018-03-14 Added input voltage protection
    [WolfDrive_H7Controller.sch]
2018-03-14 Amended input protection
    [WolfDrive_H7Controller.sch]
2018-03-14 updated footprints
    [WolfDrive_H7Controller.sch]
2018-03-14 fixed duplicate gates in U10
    [WolfDrive_H7Controller.sch]
2018-03-14 PCB layout progress for issues <5
    [WolfDrive_H7Controller.kicad_pcb, WolfDrive_H7Controller.sch]
2018-03-15 Major PCB layout revision for v0.2
    [WolfDrive_H7Controller.kicad_pcb, WolfDrive_H7Controller.sch]
2018-03-15 Finished layout, silk sceen amended
    [WolfDrive_H7Controller.kicad_pcb, WolfDrive_H7Controller.sch]
2018-03-15 Updated fabrication files for v0.2
    [WolfDrive_H7Controller-B.Cu.gbr, WolfDrive_H7Controller-B.Mask.gbr, WolfDrive_H7Controller-B.Paste.gbr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]
2018-03-15 Minor edits before fabricating v0.2
    [WolfDrive_H7Controller-B.Cu.gbr, WolfDrive_H7Controller-B.Mask.gbr, WolfDrive_H7Controller-B.SilkS.gbr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]
2018-03-15 Updated schematic for v0.2
2018-04-26 first steps, PWM test
    [wolfdrive_alpha Run.cfg]
2018-06-24 Firmware framework, work in progress
    [quadspi_detective.ods]
2018-06-24 Added misc drawings
    [4mm_con_cutouts.dxf, Cree_CAS325_DC_Busbars.dxf, planview.dxf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]
2018-06-24 Removed schematic copied from current sensor repo
2018-06-24 organised drawings
    [4mm_con_cutouts.dxf, Cree_CAS325_DC_Busbars.dxf, Cree_CAS325_DCholes.dxf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]
2018-06-24 removed superflous CAD/CAM files
2018-06-26 Encoder to analogue adapter code
2018-06-26 Pins amended for using DAC with SPI1
    [WolfDrive_H7_pinassignment.ods]
2018-06-26 Library fix for KiCAD v5
    [WolfDrive_H7Controller.sch]
2018-06-26 Compatibility for AkSim2 encoder, 13b ACK length
2018-06-28 Pay attention to angle error correction with switching frequency
    [userparms.h]

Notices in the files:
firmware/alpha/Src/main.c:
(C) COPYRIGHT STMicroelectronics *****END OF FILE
